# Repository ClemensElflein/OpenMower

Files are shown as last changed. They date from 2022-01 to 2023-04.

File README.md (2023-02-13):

# OpenMower - The DIY Smart Mowing Robot for Everyone

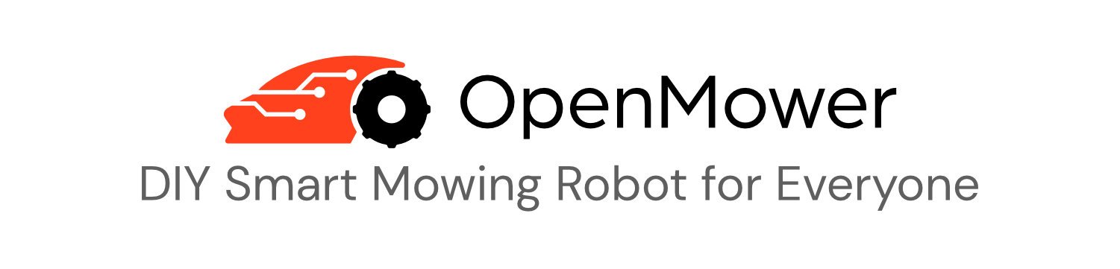
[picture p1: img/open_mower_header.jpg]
OpenMower the DIY smart robot mower
 

# Join the Discord server for OpenMower discussion: [HERE](https://discord.gg/jE7QNaSxW7)

*:warning: DISCLAIMER:**

**IF YOU ARE NOT 100% SURE WHAT YOU ARE DOING, PLEASE DON'T TRY THIS AT HOME! ASK IN [DISCORD](https://discord.gg/jE7QNaSxW7), IF YOU HAVE ANY QUESTIONS!**

# This project is active!
This is the hardware repository, so it might seem that the project is inactive, since hardware is pretty stable by now.
Most of the development work is done on the ROS code here: https://github.com/ClemensElflein/open_mower_ros

# About the Project

If you want to see a quick overview, you can check out this video:



Let's be honest: The current generation of robotic lawn mowers sucks. Basically all of these bots drive in a random direction until they hit the border of the lawn, rotate for a randomized duration and repeat. **I think we can do better!**

Therefore, we have disassembled the cheapest off-the-shelf robotic mower  we could find (YardForce Classic 500) and were surprised that the hardware itself is actually quite decent:
- Geared sensored brushless motors for the wheels
- A sensored brushless motor for the mower motor itself
- The whole construction seems robust, waterproof and all in all thought through
- All components are connected using standard connectors, therefore upgrading the hardware is easily possible.

The bottom line is: The bot itself is surprisingly high quality and doesn't need to be changed at all. **We just need some better software in there**.

## Project Goals

Here is a quick overview of this project's goals:

:heavy_check_mark: **Autonomous Lawn Mowing:** Obviously, the device should be able to mow the lawn automatically.

:heavy_check_mark: **Good Safety:** The device must be safe, e.g. emergency stop if lifted or crashed.

:heavy_check_mark: **No Perimeter Wire Needed:** We want to be flexible and support multiple mowing areas.

:heavy_check_mark: **Low Cost:** It should be cheaper than a mid range off-the-shelf product

:heavy_check_mark: **Open:** I want to share knowledge and enable others to build an OpenMower as well.

:heavy_check_mark: **Nice to Look At:** You should not be ashamed to have an OpenMower mowing your lawn.

:heavy_check_mark: **Avoid Obstacles:** The mower should detect obstacles and avoid them during mowing.

:heavy_check_mark: **Rain Detection:** The device should be able to detect bad weather conditions and pause mowing until they improve.

# Open Mower App

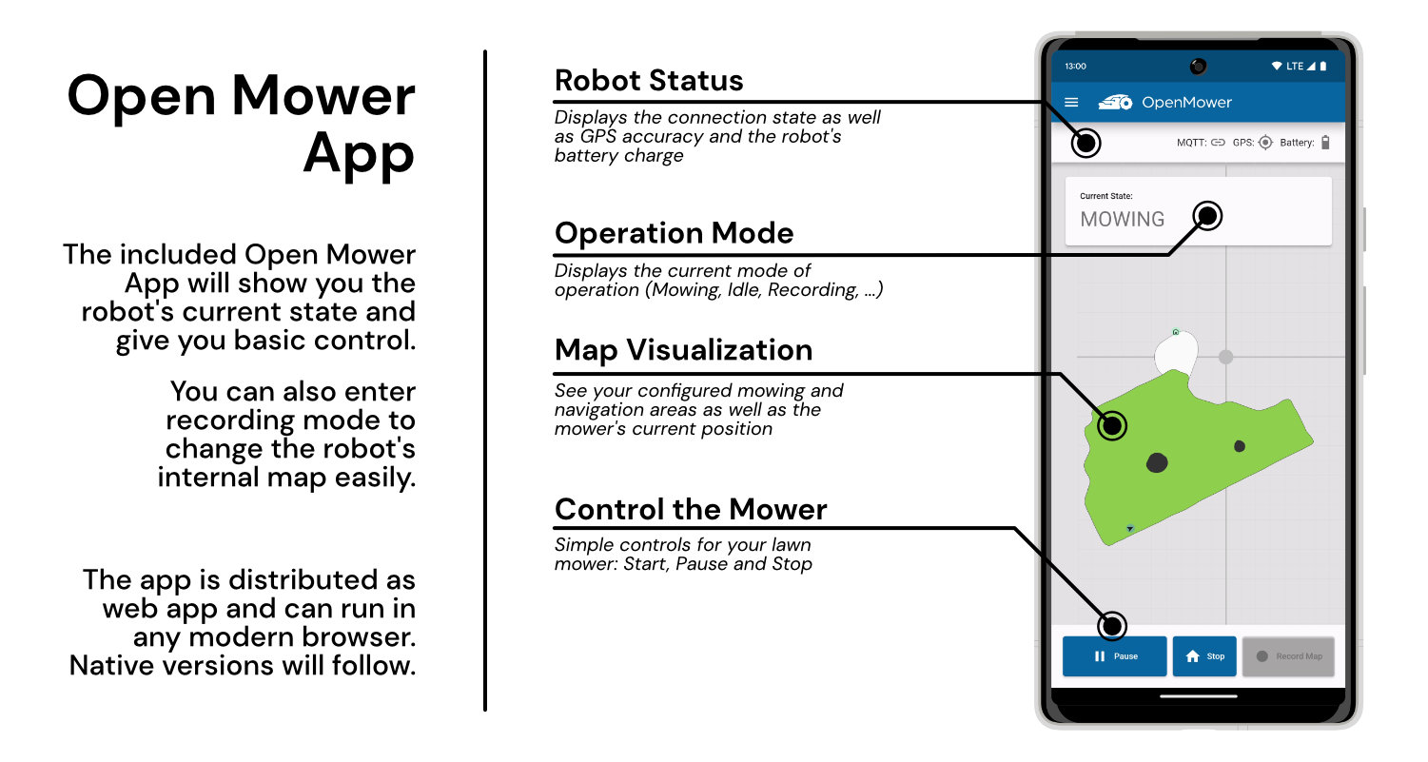
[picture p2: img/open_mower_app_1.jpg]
Open Mower App 1


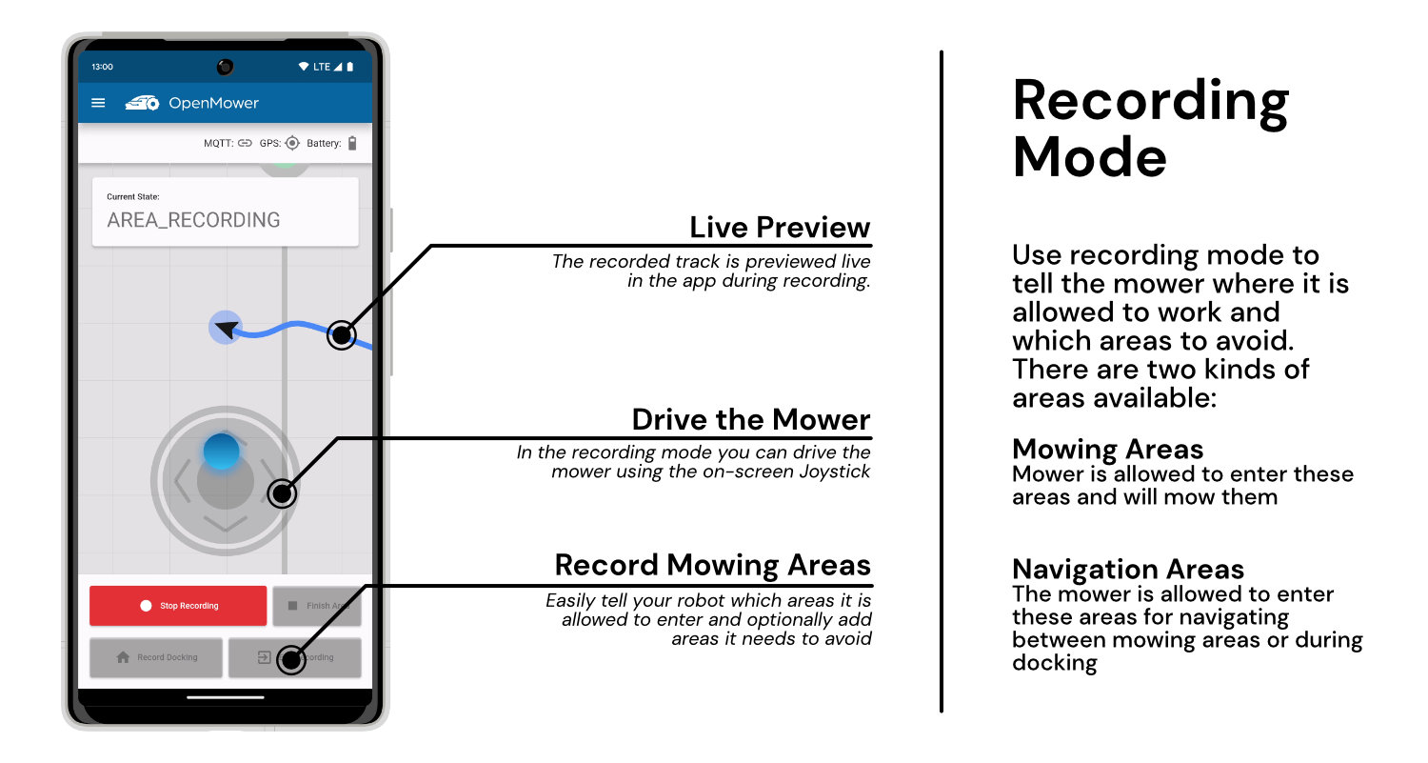
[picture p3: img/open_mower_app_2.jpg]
Open Mower App 2


## Current State

The basic mowing function finally works! As you can see in the video, map teaching and mowing work as expected. It even returns to the docking station automatically as soon as the battery gets low and continues once it's recharged.

At this point I can recommend that brave tech savvy users can build one for themselves! Since it's quite an expensive and complex project, please don't be shy and ask if you have any questions. I'm glad to help 🙂

### Hardware

By now we have a stable revision of the mainboard as well as two motor controllers to go with it. The [xESC mini](https://github.com/clemensElflein/xesc) and the [xESC 2040](https://github.com/clemensElflein/xesc2040). I'm currently using the xESC mini for my builds and it works very well. The problem with this controller is, its parts are currently hard to source. That's why we created the xESC 2040 based on the RP2040 chip. This is the low-cost variant and its support is currently experimental.

#### Hardware To-Do:

- [x] Low Level Firmware Implementation
  - [x] Voltage / Current Sense
  - [x] Emergency Stop Button tracking
  - [x] IMU Communication
  - [x] Rain Sensor
  - [x] Charging State
  - [x] Sound Module
  - [x] UI Board Communication
  - [ ] Discharge current for more accurate battery charge estimation
- [X] ROS Hardware Interface

### Software

The basic software is basically done; Our prototype works as intended (but is not able to avoid obstacles yet).

The software for the robot can be found in a separate repository: https://github.com/ClemensElflein/open_mower_ros

#### Software To-Do:

- [x] Mowing State Machine (Docking / Mowing, ...)
- [x] Path Planning
- [ ] Obstacle Avoidance
- [x] App / Visualization

## Getting Started

If you want to read how to get started building a robot for yourself, check the [OpenMower Website](https://openmower.de). There you can find information on which parts to buy, how to install the software and so on. If you find anything missing, please join the Discord server and ask there. Also there's the [OpenMower Wiki](https://wiki.openmower.de) which is written by the community. It has some additional guides and information.

# How You Can Help

You can help by starting an OpenMower build of your own. This helps to validate the concept and helps to create useful documentation for new users.

Additionally, you can help by starring 🌟 and watching 👀 this repository, since it will help with visibility. You can also subscribe to my [YouTube channel](https://youtube.com/c/ClemensElflein).

## Compatible Robotic Mowers

While disassembling the bot, I wondered about its mainboard: Instead of "YardForce" it read "GForce". After checking the internet for "GForce" robots, I found that that very similar looking robotic mowers are sold under the Herkules brand. Naturally I tried to dig deeper and actually found evidence that the mainboard is manufactured by some chinese company (SUMEC Hardware).

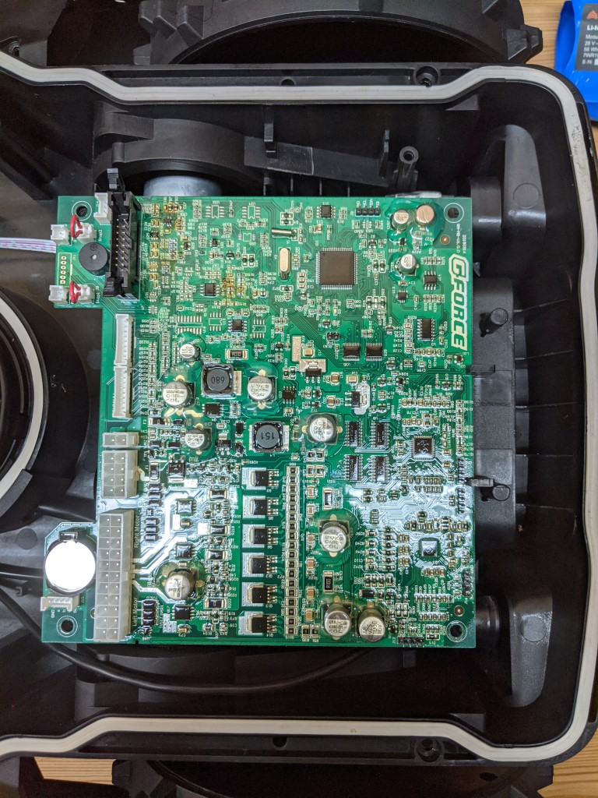
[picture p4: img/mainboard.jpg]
GForce Robot Mower Mainboard


It is therefore quite safe to assume that many robot mowers are basically the same device in a different case. This would be a huge win for the community, since this would mean that by making one of those robots smarter, we could upgrade lots of robots.

Therefore it might be a good idea to start a list of compatible devices. So if you have a cheap robotic lawn mower, you can check, if it was already disassembled in the list below. If it's not there, it would be nice of you to check, if it contains the same mainboard as ours and add your robot to the list with some some pictures / model numbers.

### List of Compatible Mowers

By now, some guys have disassembled their mowers and it doesn't look as good as I initially hoped. The GForce boards are basically just used by YardForce and some rebranded versions for the EU market. My exact hardware was only found in the mower I'm using (YardForce Classic 500) and in recently manufactured SA650 ECOs. The SA650 has a different chassis and we don't have a way of mounting the GPS antenna yet. Therefore at the moment, the only compatible mower is mine (the YardForce Classic 500). 

If you want to have a look at the disassembled mowers, check the Google Docs [here](https://docs.google.com/spreadsheets/d/1BX0-KEs5v-VED8-RA4BLE-wRdXHtlmcKy4n9K5vJVAA)

# More Infos

This page only contains the basic overview of the project. To follow my current development state, check out my [Blog](https://x-tech.online/).

# Patents, Local Laws, Liability
Before building a robot based on the designs published here, please make sure that you are allowed to do so in your specific regions.
There may be patents and / or laws prohibiting you of doing so.

The code/schematics/PCB files are distributed in the hope that it will be useful, but WITHOUT ANY WARRANTY; without even the implied warranty of MERCHANTABILITY or FITNESS FOR A PARTICULAR PURPOSE.

This basically means: I'm just documenting a project of mine here for free and I don't have the time and resources to check that devices built using this information will be safe to use, legal to use or even work as intended. You will need technical know-how to use this project and I'm not liable for any damages your devices do to anyone or anything.

# License

<br />This work is licensed under a <a rel="license" href="http://creativecommons.org/licenses/by-nc-sa/4.0/">Creative Commons Attribution-NonCommercial-ShareAlike 4.0 International License</a>.

Feel free to use the design in your private/educational projects, but don't try to sell the design or products based on it without getting my consent first. The idea here is to share knowledge, not to enable others to simply sell my work. Thank you for understanding.

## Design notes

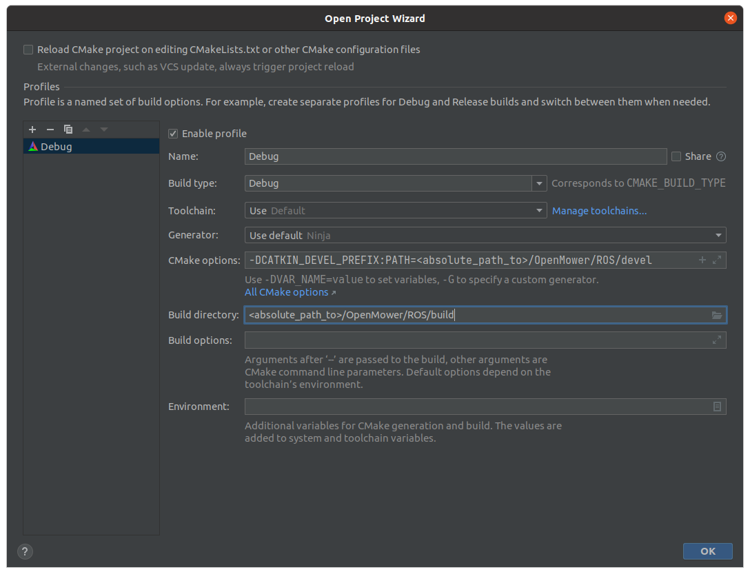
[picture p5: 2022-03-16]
img/clion_cmake_settings.png

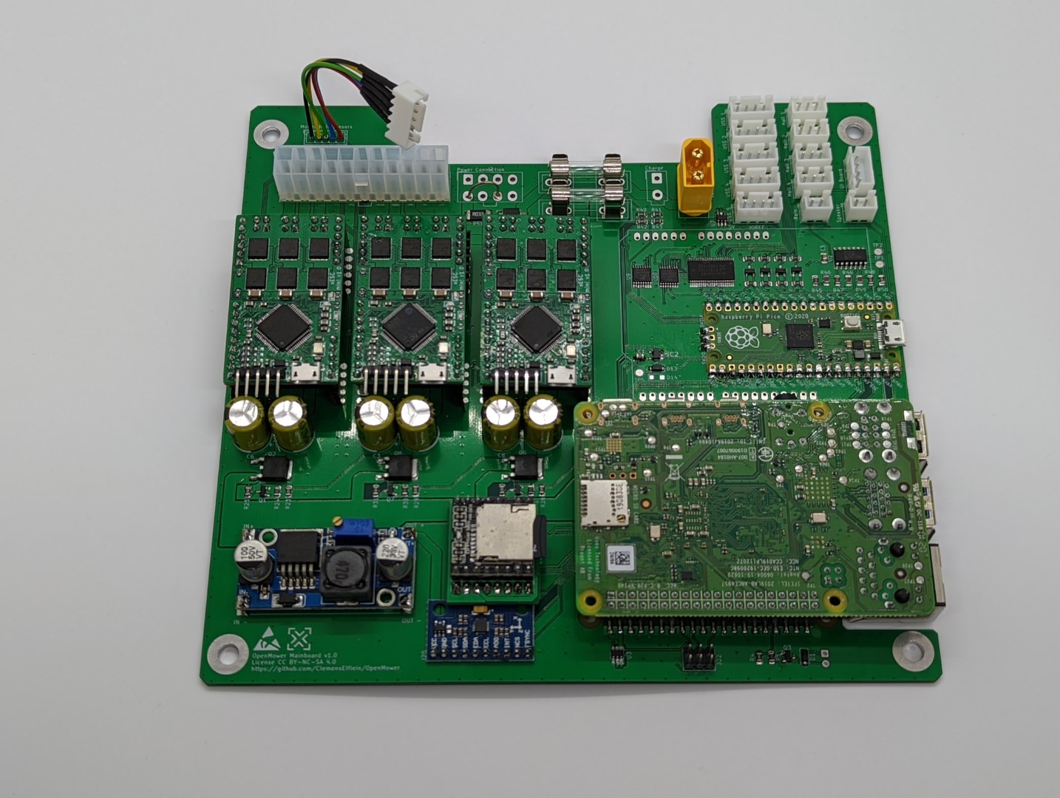
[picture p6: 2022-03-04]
img/open_mower_mainboard.jpg

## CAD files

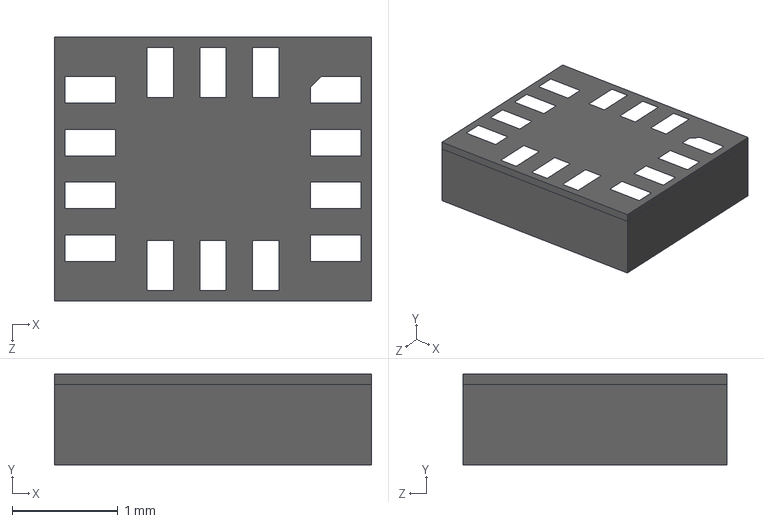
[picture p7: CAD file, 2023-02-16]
Hardware/OpenMowerMainboard/LSM6DSOTR/LSM6DSOTR.stp
3.00 x 0.86 x 2.50 mm

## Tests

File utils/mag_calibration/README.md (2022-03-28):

# Magnetometer Calibration

In an ideal word, when we rotate our robot around the Z axis, our magnetometer values would create a circle around the origin. Unfortunately, in the real world, due to magnetic fields in the robot and sensor bias, this is **not the case**. The magnetometer will most likely be an ellipse or a circle with some offset from the origin.

**This calibration will remove this offset, but won't remove any elliptical form!**

## How I'm currently doing this

Currently, I am doing it in the following way:

1. Put the robot in your lawn (turned on, fully assembled)
2. Start a teleop + recording session. Rotate the robot slowly in one spot for several rotations.
3. Run the plot_mag.sh script: `./plot_mag.sh /path/to/your.bag`
4. Check in the interactive plot, if your values are circular and if the fitted circle (red circle) is a good fit.
5. If everything seems fine, your bias values will be printed in the console (see example below).

## Example

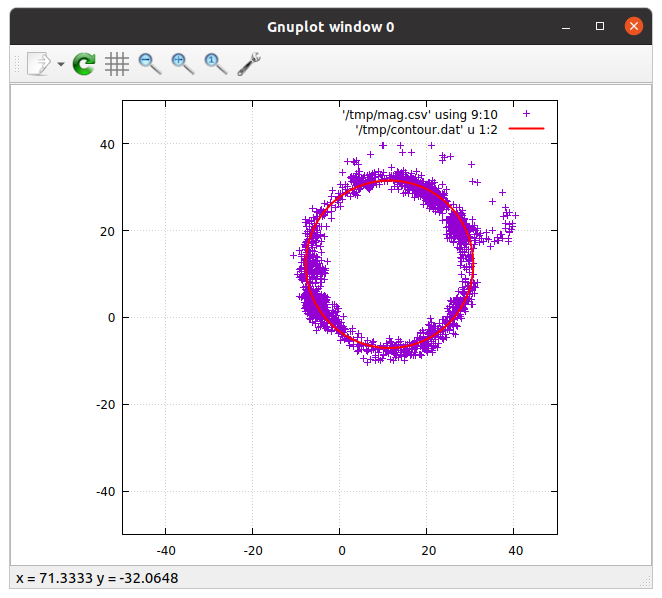
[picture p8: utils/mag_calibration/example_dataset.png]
example_dataset


This is the output of my calibration run today.

Note that:

1. The outliers have been rejected
2. The plot is pretty much a circle, moved to the upper right hand side

The console output was the following:

```bash
[...]

After 3 iterations the fit converged.
final sum of squares of residuals : 8.48886e+07
rel. change during last iteration : -4.36383e-06

degrees of freedom    (FIT_NDF)                        : 16540
rms of residuals      (FIT_STDFIT) = sqrt(WSSR/ndf)    : 71.6402
variance of residuals (reduced chisquare) = WSSR/ndf   : 5132.32

Final set of parameters            Asymptotic Standard Error
=======================            ==========================
bx              = 11.4452          +/- 0.0209       (0.1826%)
by              = 12.2336          +/- 0.02425      (0.1982%)
r               = 370.698          +/- 0.5595       (0.1509%)

correlation matrix of the fit parameters:
                bx     by     r      
bx              1.000 
by             -0.402  1.000 
r               0.092 -0.020  1.000 
```

**--> Our bias parameters (bx, by) are 11.4452 and 12.2336**

## Better Calibration

This assumes that the result will be a circle with an offset. In reality, the result could be an ellipse. Also it would be nice to automate this process.

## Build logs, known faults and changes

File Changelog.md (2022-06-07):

# Changelog

## [current dev progress]

#### Hardware

- Added solder jumper so that we don't need to solder some ICs if we don't need ultrasonic and sound
- Moved some solder jumpers to the bottom of the board to keep them accessible even with IMU mounted.

#### Software

##### Breaking Changes

- Moved most of the configuration to an external file
- Removed start and pause mowing from rosparams. This was just a hack to trigger it using rqt_reconfigure.
- Removed area_recorder and corresponding configs
- Added SensorFusion with imu_filter_madgwick, you need to set your mag biases in the global settings file now

##### Features

- Added UI Board integration to LowLevel Firmware
- Added service to start and pause mowing as well as start area recording mode
- Added area recording behavior to main logic, so that we don't need an additional launch file for it
- Added a mower_logic/current_state topic which has the identifier of the current high level state.
- mower_comms now listens for UI button messages and calls the high level control service accordingly.
- Added support for LAT/LNG coordinates instead of relative coordinates. Set **OM_USE_RELATIVE_POSITION** to **false** for this and provide an origin for your local coordinate space using **OM_DATUM_LAT** and **OM_DATUM_LONG** in your local config file.
- Added the mag_calibration node to help magnetometer calibration without manually recording and copying files.

##### Small Fixes

- Changed planner logic, so that it starts with innermost outlines

- We can now configure arbitrarily many outlines
- Motor temperatures can be configured
- Added safety offset parameter to the outline (i.e. shrink area without rerecording the areas)
- Added vesc_msgs to mower_msgs to resolve a dependency issue

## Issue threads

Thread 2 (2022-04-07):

Website SSL Error

admbradford, 2022-04-07:
Receiving an `ERR_SSL_PROTOCOL_ERROR` when visiting your blog site https://x-tech.online/

ClemensElflein, 2022-04-07:
Thank you for the report. It's working fine for me even in a private tab. Which browser are you using? What's the error message you're getting?

admbradford, 2022-04-08:
I’m on mobile chrome v100.0.4896.77 iOS 15.4.1

here’s a screen shot

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

admbradford, 2022-04-08:
I checked off my home network and it worked fine, I have some aggressive protection from my router. It’s likely due to the second cert

[SSL Server Test: x-tech.online (Powered by Qualys….pdf](https://github.com/ClemensElflein/OpenMower/files/8451909/SSL.Server.Test.x-tech.online.Powered.by.Qualys.pdf)

ClemensElflein, 2022-04-08:
Thank you for the info! I'm looking into it. To be honest, I'm just using the Let's Encrypt Certbot and was glad that it seemed to work out. There has to be some strange configuration still.

Closed 2022-09-22.

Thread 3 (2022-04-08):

Option to mow in a randomized pattern?

jh83, 2022-04-08:
Is it possible to have the mower to cut the grass in a randomized pattern  and only use the perimeter as a "limit" for which it should stay within?

Having the mower cut on the same lines over and over again will create track's in the lawn. There is a reason to why husqvarna has spent a lot of time developing how the robot should find its way back to the charger, where it actually varies its distance to the perimeter cable to avoid creating track's.

Husqvarna has now released a gps rtk version of its automower (which is very expensive) and I think that stiga will release one soon as well.  As far as I know, this still cut in a randomized pattern, while using gps for the perimeter limits.

Very good project though!

R5fan, 2022-04-11:
If you want to avoid making "tracks" or stripes (which many people try to make on purpose btw), the much better solution is not reverting to random navigation, but randomizing either the starting point (so tracks are offset a bit on each session, although with the narrow mowing width of most robots that may not yield much) or rotate the orientation of the tracks by a random angle.

jh83, 2022-04-11:
A robotic lawn mower does not create the "stripes" which many People (including me) like even if it would cut in a straight pattern.

I agree on the inefficiency in the randomized pattern. But there is a reason to why the GPS mowers are sticking to the randomized (which not really is randomized) pattern on their rtk-gps models.

A robotic lawn mower, when used as intended, creates a much nicer lawn compared to a normal cutter. The reason behind it is that the robotic "always" cuts and does it from different angles. Moss and other none-grass things does not like it, and is replaced by the grass. - So there are different views on what a robotic cutter is, if it is intended to cut the lawn as quickly as possible, or if it is intended to "take care" of the lawn.

If running on straight lines, then care needs yo be taken to the uncut grass that remains when the wheel presses down rhe grass, and then is unable to cut that grass on the next line and so on.

Here is an interesting article on the line vs random cutting. It says that there is only a 30% time difference between the two. https://robolever.com/random-vs-systematic-robotic-mowers-which-is-better/

As said. We like things differently, so If it would be possible to run either straight lines, or in a random pattern and use gps for perimeter then it would be great

pbs-websuntangled, 2022-04-11:
Agreed 👍

R5fan, 2022-04-11:
Mowing from random angles matters, but systematic mowing with a randomly rotated pattern every session would yield the same result. I dont see the downside. Heck, since his code uses slic3r code, you can even use any other infill pattern you want, plenty to chose from, all of them far more efficient than random.

Speaking of efficiency, if you have a square lawn with no obstacles, _maybe_ the 30% less efficient claim is right, but for sure its not in my garden, where my robot can mow for 3-4-5 days and still not cover every patch. If it mowed systematically, knowing its width and estimating speed, I guess it would take ~3-4 hours?  Even if its 24hr, that is a massive difference. I used to have a random navigation robot vacuum, and that is okay, because you cant tell if it "missed" a spot for a few days. Lawn mower is different, if you cant mow for a week due to rainfall, and then it takes almost a week before the robot to "catch up" and get everywhere. So during that  week you will have patches of freshly mowed grass next to nearly 2 week growth, not very pretty. More than once I took my old mower and mowed my lawn by hand to avoid exactly that.

Anyway, if that is what you want, who am I to stop you, but it makes no sense to me.

pbs-websuntangled, 2022-04-11:
For me the point is not so much about wanting randomness

Rather it's good to cut the grass from different angles with different patterns

It's definitely true that for real world lawns, it can be 4 or 5 days of permanent mowing before the same hit is hit twice

Structured mowing with  rotated efficient row by row mowing would be a great feature

This project is amazing 👍👍👍

R5fan, 2022-04-11:
> Structured mowing with rotated efficient row by row mowing would be a great feature

Agreed! Because random navigation doesnt result in even distribution. To illustrate, here is my back lawn:
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
The visible tracks give a hint (I would really LOVE to create a coverage map somehow from my timelapses, or even be able to simulate random navigation on my lawn and see the result, im just curious what the coverage looks like, and I know its not evenly distributed);  the mower will cross the center of the image dozens of times before ever reaching the left corner. I also really do not like the "look" of those tracks. They fade, but if you mow every day, they are there every day especially if its a bit humid.

kevinmce, 2023-06-30:
There is a mow pattern orientation in the mower config, this should be relatively easy to have randomized at the start of each mow should the user input that option.

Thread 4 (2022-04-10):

How to start ti build the more?

chicco83, 2022-04-10:
Hi.
I'm very interested in the project but It Is not clear how to start the hardware part. Which parts to buy, if It Is mandatory to have a dedicated PCB produced ecc

r00li, 2022-04-13:
Yeah I too would be interested in a bit more detailed guide of what exactly needs to be purchased, which PCBs made, ...

I had a look at the BOM and it seems a bit incomplete - it seems to only cover the main board components, but doesn't include things like the GPS receiver, ...

GruNyv, 2022-04-16:
Based on the video he posted, the gps receiver is a simplertk2b (with a zed-f9p GNSS module) and a u-blox multiband antenna. These are relatively cheap, around 200 euros, considering that other brands usually cost several thousand euros.

Kisses99, 2022-04-17:
Maybe it's even cheaper to hook up an old smartphone.

GruNyv, 2022-04-17:
@Kisses99 The problem is that your smartphone is not RTK compatible. You need a GNSS module that supports RTK, such as the ZED-F9P.

Kisses99, 2022-04-17:
Ah got it.

GruNyv, 2022-04-17:
Yes, the cost of RTK certainly is a barrier to entry. This was especially true before the ZED-F9P, where it was mostly reserved for the industry and extreme hobbyists. Another issue is that you might need 2 of them, where one acts as a base station, if there are no freely available base stations near you through i.e. RTK2GO and you don't want to pay for a commerical subscription

FadeFx, 2022-04-17:
@Kisses99 there are cheaper optiins as well, but i guess they dont provide enough precission for a task like that. Did you ever check the precission of your smartphone gps? its most likely not below 5m...

GruNyv, 2022-04-17:
Unless you use some sort of differential gnss (which RTK is a subgroup of), you can't expect better accuracy than 3-10 meters depending on the conditions

Kisses99, 2022-04-17:
@FadeFx right that's what I just figured.  However I'm still concerned that gps accuracy may be significantly impacted by shades of trees.  For an open yard this may just be fine.

GruNyv, 2022-04-17:
Yes, the tree shades and building is what I am concerned with. I have been working with this exact model during this spring and it often has troubles when you enter non-open areas

FadeFx, 2022-04-17:
could it be possible to compensate this by also taking in account your actual movement?

GruNyv, 2022-04-17:
You certainly can predict your movement using multiple sensors using a kalman filter. However, it might work to simply drive randomly when you are in a region without signal, since this is what they already do. The issue is of course the possible lack of boundary wire

mischla, 2022-04-17:
> Yes, the cost of RTK certainly is a barrier to entry. This was especially true before the ZED-F9P, where it was mostly reserved for the industry and extreme hobbyists. Another issue is that you might need 2 of them, where one acts as a base station, if there are no freely available base stations near you through i.e. RTK2GO and you don't want to pay for a commerical subscription

Is the German SAPOS system which provides Ntrip in RTCM 3.1 format what would be needed here?

GruNyv, 2022-04-17:
@mischla Most network RTK providers which uses RTCM 3 should work, but you should check out which satellite configurations they provide corrections for (GPS, Galileo, GLONASS...)

mischla, 2022-04-18:
Thanks for the quick answer, in this case all of them.
Link below in German valid for NRW: https://gppspro.saposnrw.de/service.php

stilsch, 2022-04-18:
Maybe a look at ardumower.de and it's Sunray (GPS-RTK) firmware might also help you https://github.com/Ardumower/Sunray

Bojkas1985, 2022-04-19:
Hi, wouldn't some form of triangulation using bluetooth iBeacon be possible?

fsommer1968, 2022-04-19:
> Hi, wouldn't some form of triangulation using bluetooth iBeacon be possible?

What is the accuracy you can achieve?
Everything more than a few (more than 10cm) over the complete backyard is just not acceptable!

GruNyv, 2022-04-19:
From what I could find on the Internet, the accuracy is at best one meter, which is not good enough to be used for control. Could maybe be used as a backup if you add a safety zone on 1 meter from the perimeter when you don't have RTK, but it will of course increase the already pretty expensive build

lightheaded, 2022-08-07:
Hi! Coming back to the initial question, would it be possible to add a "getting started" section to the readme? I have extensive software background and I tinker with some electronics, but I've never created my own PCB. Looking at the project, I have the same problem as @chicco83 - where to start?

vamatis, 2022-08-10:
Have a look at the wiki. Most of the needed infos are there...
If in doubt, just ask in the discord

lightheaded, 2022-08-10:
Thanks for pointing me that way! Here's the link for those still lost: https://wiki.openmower.de/index.php?title=Main_Page#How_to_Get_Started

rfvermut, 2023-02-13:
There is a better guide now: https://openmower.de/docs/getting-started/

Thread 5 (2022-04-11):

WORX Landroid M WR140

TonyBrobston, 2022-04-11:
> Naturally I tried to dig deeper and actually found evidence that the mainboard is manufactured by some chinese company (SUMTEC Hardware).

This part of the readme got me curious to checkout the board in my WORX Landroid M WR140.

It looks like it's a completely different board; however, I figured since I took the pictures, I mine as well post them in case this mower can somehow be supported. If that is the case, I'm definitely interested in getting off Worx horrible software, it is quite unimpressive.

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

unreality, 2022-04-14:
Depending on whether that ESP32 runs the whole thing or just provides wifi/bluetooth connectivity you could reflash it quite easily with custom firmware.

The ESP32 is reasonably powerful for an embedded soc.

LTKingChaos, 2022-04-16:
I would also like custom firmware for the Landroid. Factory firmware sucks bigtime.

hugokernel, 2022-04-20:
Thank you for the pictures @TonyBrobston

I'm also very interested in an Opensource version of a Landroid (WR155 / L2000) in order to perpetuate the use of my robot and to bring additional features.

Seeing the electronic board and the fact that the board is embedded in resin will make it very difficult to repair.

The LandLord project (https://github.com/Damme/LandLord and https://hackaday.io/project/6717-project-landlord) is trying to produce an Opensource software for Worx robots (specifically the wg79X).

Damme, 2022-04-20:
Btw, the cpu is a LPC1768 under the goop (epoxy?)

RFBomb, 2022-05-06:
I have a 2021/22 model WR147 (with the radial dial for menu navigation), and I am also interested in this project. I also have the ACS unit installed, so support for that would be a must.

Michael-Bischof, 2022-05-07:
Also super interested in flashing custom firmware on the worx robot. I have the Landroid L (WR148E) and would also be into modding it. Can‘t get worse than it is right now software wise 😅

JochenKr, 2022-05-11:
Any chance that LandLord project and OpenMower will be combined?
OpenMower idea to use Rpi with good GPS is fantastic. This in combination with a simple modification of the Worx Landroid e.g. just connecting the Rpi to the original MCU to give the commands to the robot, would be a great simplification and super cost efficient

MBischof-gcx, 2022-05-11:
Already happening ;) See https://github.com/Damme/LandLord/issues/5

endoskop27, 2022-05-23:
Hi @TonyBrobston! Is there any Letters/Numbers printed on the big Controller on the Board (not the ESP32)?
On the pictures it is quite invisible

chopperpl, 2023-05-08:
Is this still alive? I would love to jump on the wagon, but it seems the shortage of RP boards and its price spike have killed the project.

mangeamg, 2023-05-24:
Why not use a cheap RPi clone, like orange?

scigany, 2023-07-12:
Hi,
does anyone have a diagram where I can identify the two elements marked with an arrow that are burnt in mine?
burned a hole in them,

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

Jmaxime89, 2023-07-29:
Hello ! I too would be sooo interested in supporting the landroid.

I keep an eye on the projet since a long time but the yard force is very hard to source in canada

pawster-hub, 2023-08-04:
Good morning,
I have a pcb in front of me with fried components. Can someone give the symbols of the elements t9, t10, t? (left of connector), d5, ic9? Hopefully I'll be able to do something more with it. Regards
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

shagi898, 2024-05-25:
Hi. someone found ic9
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

iLLiac4, 2024-06-09:
What is the purpose of this IC. The problem is that even when robot is turned off with the inserted battery the chip consumes power. I have checked it with thermal camera. This ic gets at around 30-40C. Also the coil gets a little warm. The problem is that it drains the battery even when not doing anything. Worx batteries has no overdischarge protection in them so it drains them fully.

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

Andy617237, 2025-03-24:
> Hi. someone found ic9 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

Hello, Someone find what is iC9 my is burned ;-(

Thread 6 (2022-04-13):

Alternative to custom PCB

conradkirschner, 2022-04-13:
Is there a possibility to remove the custom PCB and use "standard components" e.g. pi cluster ?

This would enable more people in development.

fsommer1968, 2022-04-13:
You have to integrate with the remaining parts like left drive, right drive, cut engine. I´m not aware of a pi that can direct connect :-) Therefore at some point you always need an integration component, you name it "custom PCB". I applaud the effort building the PCB because I´m sure it costs a lot of money.

conradkirschner, 2022-04-13:
Would be cool to have the research material why a custom PCB was required and where it could be possibily replaced.

I defenitly see the reason to use a custom PCB, it's just for enabling more devs if this step would be optional for production use ;)

r00li, 2022-04-13:
I mean these days where you can get a custom PCB made for like 5$ (a bit more for bigger ones, but still not that much) it's a no-brainer that a custom PCB will be used. I don't see why one would even want to go towards a different route.

ClemensElflein, 2022-04-13:
I agree, it's an obvious choice here. We need to connect hardware of some kind to interface with the robot and we need it to fit a predefined space. A custom PCB provides all that for very cheap.
I know that not everyone is willing to solder the SMD components, but that's a completely different issue. At the moment this is very much R&D so there's no way around it.

Closed 2022-04-13.

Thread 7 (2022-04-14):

Perimeters

nyxtom, 2022-04-14:
One issue that you may run into is that typically front lawns have neighboring lawns that you *would* want to designate a perimeter/border on. That being said being able to do this from the phone (i.e. AR) rather than wires would be preferred.

ClemensElflein, 2022-04-28:
You are able to set a perimeter by driving around it. Check the YouTube video for a demo: https://www.youtube.com/watch?v=BSF04i3zNGw

It's not as fancy as an AR app, but it works well for defining a boundary.

I'll let this open as a feature request, though.

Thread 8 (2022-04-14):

US/North American source for compatible base hardware?

aderusha, 2022-04-14:
As noted in the README, the existing platform is the Yard Force Classic 500 which comes from a Chinese OEM [SUMEC Hardware and Tools](https://www.sumecpower.com/) which itself is a subsidiary of [SINOMACH](http://www.sinomach.com.cn/en/).  Their ["Brand" page](https://www.sumecpower.com/brand) lists G-Force, Yard Force, and PowerG.  PowerG looks to be battery powered hand tools, which leaves the G-Force and Yard Force side of things.

## Yard Force USA

The Canadian and US links from the SUMEC page bring you to [YardForceUSA.com](https://www.yardforceusa.com/).  They have a [Robot Mower product page](https://www.yardforceusa.com/robot-lawn-mowers) with two products listed, the RVX4E and RVX4.  I can find no mention of these devices being made available for sale anywhere.  I've emailed the US distributor and will update if I get an answer back.  I eventually found [an online shop for Yard Force tools in the US](https://sumec.mybigcommerce.com/force-tools/) but no robot mowers are listed.

The [international page for Yard Force](https://www.yardforce-tools.com/PC_Web/International/HTML/Products.html) lists different models than the NA page, and that includes a model [SA500ECO](https://www.yardforce-tools.com/PC_Web/International/HTML/Products_parameter.html?id=598) which bears a passing resemblance to the Classic 500 (as well as being suspiciously similarly named).  [Amazon in the UK](https://www.amazon.co.uk/Yard-Force-Robomower-Lithium-Ion-SA500ECO/dp/B07B6WHCYQ) shows this model as no longer available and it appears to be an older 2018 device which they possibly are no longer making.

## G-Force

This line is harder to pin down.  [The product page](https://www.gforce-tools.com/en/RoboticMower-26.html) shows a handful of models, but I cannot find any listings for these mowers on sale anywhere.  [Product videos I've found are from 2015](https://www.youtube.com/watch?v=HbvwlFQ7TGM), so this might be an older line of devices.

---

If anyone else has any ideas as how to obtain a suitable mower deck in the US, post here and we can all get to hackin'!

llama, 2022-04-22:
I am planning to order from [amazon.de](https://www.amazon.de/M%C3%A4hroboter-Classic-500-Kantenschneide-Funktion-Wochentags-Bedienfeld/dp/B08H1Y3KXZ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)  and use [mygermany.com](https://account.mygermany.com/web/content/new-register?canvassID=cdbe1208-010e-47b1-9c4d-8b1bb678f9e4) to forward the package.

The question I have: do all of the models on that Amazon.de page work with OpenMower? Or should I buy the "Classic 500" to exactly match what @ClemensElflein has done.

rjt, 2022-05-25:
$590 New up on eBay.  Buying thru PayPal may offer some protection even though [drahman7](https://www.ebay.com/usr/drahman7/) is a member of this project.  [https://www.ebay.com/itm/304477543176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](YARD FORCE robot lawn mower Classic 500, 500 m², 40% incline, works w OpenMower)

[https://www.ebay.com/itm/304477543176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](https://www.ebay.com/itm/304477543176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)

darkmastermindz, 2023-04-14:
Any updates on this?

ffries, 2023-07-10:
If you visit Amazon in France, you should be able to find the product number (ASIN). I did the converse many times. The ASIN number is B09RFVFV1C. Then connect amazon.fr and try to buy it.

Here is a full URL:
https://www.amazon.fr/Yard-Force-Tondeuse-Classic-Bluetooth/dp/B09RFVFV1C/

Please note that I did not purchase it myself and I am still waiting.

symmatree, 2024-04-15:
I can't find the Yard Force 500 Classic for sale on any site now. I'd guess some other chassis would work but it's not at all clear how to validate that?

liquidbear99, 2024-08-03:
@symmatree I also am unable to see it sold anywhere
on any site. (North America or Europe) The classic 500 may be discontinued.

mpcathey, 2025-06-26:
I'm in the same boat.  Has anyone else had better luck?

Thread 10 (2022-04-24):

Avoid filesystem corruption

vguttmann, 2022-04-24:
I would very much like to build the mower and help with development, but for me to build it, it needs to be foolproof long-term, as I will be moving out soon, and I don't think my parents have any interest in reinstalling the operating system on their lawn mower.

Raspberry Pis have a history of corrupting the file system on their SD cards, so I'd like to know if there are any mitigations for this, and if not, advocate for their implementation.

Schaumi19, 2022-04-25:
As far as I know the OS is still Raspbian with ROS installed. The Problem with the SD-card is writing and in Raspbian there is a option to not write to SD. If that is selected it writes only to the RAM so if there is a power loss the system is set back to the point the option was selected.
Hope it helps

noobydp, 2022-04-29:
I got bored and read up on this problem, so I'm no expert.

[This article](https://hackaday.com/2022/03/09/raspberry-pi-and-the-story-of-sd-card-corruption/) suggests the problem has been resolved and may have been due to bad rpi hardware or cheap sd cards.

I've used 3 or 4 pi's over the past few years starting with a Pi B, and I've never had an issue.
I've always Used genuine samdisk cards, not sure if it helps.

That said the overlay fs/ read only sd card mode is handled at the os level in raspbian so might be an option.

scottishjohn1982, 2022-04-29:
The Amazon warehouses in the us are full o of "legitimate" sd cards from
major brands that are actually produced there manufacturer but are part of
lots that failed qc and somehow (through illustrated supply chains) work
their way in to the Amazon warehouses and get mixed back into the
legitimate supply chain.

I have a stack of sd cards that I paid good money for that I only used for
projects that can run in read only mode.

There were issues with the older pis that could easily corrupt quality sd
cards, but those have been resolved.

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

Schaumi19, 2022-04-29:
It is true that you have less problems with genuine sdcards whatever brand, but it is also a fakt that the life time of an sd card is limited tue to the write cycles(up to 10k some sources say 100k). Thats why the problem is not the normal usage. But if there is something like a log file that gets written every second you are done afer a few days. Or if the file gets writen less the problem occers afer a longer period of time what could be worse.

FilipBE, 2022-04-30:
Some Raspberry Pi Compute Module 4 (CM4) boards come with a built-in eMMC flash chip for storing nonvolatile data. This chip replaces the need for a separate SD card, which can be useful if you want to avoid the use of SD cards.

JoeKae, 2022-04-30:
Just boot from a small ssd via usb. They last much longer than sdcards or emmc.

FadeFx, 2022-04-30:
i am not sure if adding an ssd inside the smal case of a mower.

JoeKae, 2022-04-30:
You can use small m2 type ssds.

vguttmann, 2022-04-30:
I did open this issue because I had a (as far as I can tell) genuine Samsung 64GB SD card go bad in a Pi that a personal project ran on.

I would agree that a CM4-based mower sounds like a good idea, given the onboard eMMC flash, and that it is intended with use in industrial settings in mind. Of course, that would mean sacrificing USB 3.0 connectivity, but as far as I can see, that's not really used here.
The CM4 DOES have a USB 2.0 interface, so no USB controller on the board would be necessary.

pedromorgan, 2022-05-04:
At end of day we want machine to be 100% reliable.. with ..a failover etc...(line replacable)

maybe an SD raid ? or ssd RAID ?
as @JoeKae mentions, the m2 ssd's could be useful.. but expensive..

or a stpuid raid..
https://hackaday.com/2018/02/12/worlds-stupidest-solid-state-disk-drive-hack/

Schaumi19, 2022-05-05:
ssds last longer but have the same problem. So just dont write do the ssd/sd or only write every few days. I don't think it is a real problem, that it gets reset a few days if the battery dies.

wooter, 2022-06-21:
I've been using [Log2Ram](https://github.com/azlux/log2ram), and endurance type SD cards. None of them have failed yet, in other applications like RPi dash cams and power monitoring.

ClemensElflein, 2022-06-21:
We're working on having the software as docker images, so that we can use Raspbian as base system. This would allow us to use the overlayfs setting in raspi-config which should fix the sd corruption problem without much work.

plopaur, 2022-08-08:
I would recommend looking at Tinycore Linux for Rasperry Pi. This is a minimal ramdisk only distribution with no automatic writing to sdcard which i have used in the past. A new package for openmower has to be created.
Configuration changes can be written to sdcard instantly.

http://www.tinycorelinux.net/ports.html

docgalaxyblock, 2022-08-31:
@plopaur I could not find any information if ROS runs on TinyCore. If it does and it is stable that may be a way to do it

@vguttmann @pedromorgan I am planning to build my mower based on a CM4 w/ emmc and [this adapter](https://waveshare.com/wiki/CM4-IO-BASE-A) - It has a M.2 2230/42 slot too but I think a ssd is an overkill

It will take some time cause I accidentally ordered a CM4 w/o wifi so I am returning it and need to wait until my desired variant is available again.
Also I plan to take a look around the OS side of the project
*Stay tuned* 🤗

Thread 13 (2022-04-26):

Cutting grass in different pathways

Frosty21, 2022-04-26:
More of a feature idea but when cutting grass you wouldn't want it to cut the grass the same way every time. So cutting it at 4 different angles (horizontal, vertical and diagonals) would be a good idea. That way you avoid ruts [ref](https://www.scotts.com/en-ca/library/spreaders-mowing-tools/how-mow-lawn-lawn-mowing-tips-tricks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,forming%20ruts%20in%20the%20lawn.) [ref2](https://blog.davey.com/2019/08/should-i-alternate-directions-each-time-i-mow/)

dunno how you would implement this but if I have time later in the year I look into it from your code.

btw nice work @ClemensElflein . Maybe from this we can implement this as a snow remover (just an idea on top of this way out of left field...). would be cool if you could add another motor to horizontal attaching a snowblower scraper and the flat motor as a fan blower with a controlled vent that could store the snow in a certain area.

patrickdk77, 2022-04-29:
Is the gps accurate enough that it would ride in the same 1" wheel width track each mowing? Relative accuracy is pretty good, for position of a single mowing, but between days, or even hours, it should drift by a good foot or so, causing it to not rut.

staysayo, 2022-05-08:
Yes, it's very accurate because he's using RTK positioning that's accurate to 2 - 5cm (3/4" - 2").

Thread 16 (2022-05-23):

Enable Low Level Emergency Deactivation (Button)

endoskop27, 2022-05-23:
**Problem Statement:**
Since the Mainboard of the Robotic Mower has been substituted the emergency Stop button functionality is assumed not to be working. This part is one of the most important safety measures beside the Gyroscope based deactivation of the mower, I propose to integrate a low-level emergency switch which deactivates the Motors.

Expected Behavior:
- If Emergency Button is pressed the Robot stops mowing instantly and requires manual reset
- The low Level Controller (PiCO or similar) requires an reinitialization routine from Raspberry in order to restart operation
- Saving the location and time of event on storage

Proposed approaches:
- Hardware based Kill-switch cutting the motor driver voltages
- Software based ISR listening on the Emergency Button Pin and actively deactivates motors

ClemensElflein, 2023-06-28:
your assumption is wrong, the emergency button works as you describe. mower goes into emergency and needs to be unlocked manually

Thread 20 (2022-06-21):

Versioning / Branches / Releases

ClemensElflein, 2022-06-21:
At this point it would be nice to think about release + versioning, since it's not optimal right now.

**Current State**
Currently, I'm just pushing updates and we're using the latest development state. This is fine for now, because I try to only push things that are working, but in the future it might be nice to have a "stable" release.

**Goal**
Since the OpenMower is basically two components, the hardware and the software, it would be nice to have a versioning system which shows which hardware version works with which software version.

Also it would also be nice to provide a packaged bundle of hardware (BOM, Gerbers,...) and software (precompiled image).

**Progress**
**Vermut** on my Discord is working on streamlining the KiCAD releases and **jakub** is working on streamlining software releases.

Currently the idea for hardware is to have a GitHub action which checks DRC, packs gerbers, generates iBOM, etc. This solves the problem of people just wanting to get Gerbers + BOM to order the PCBs without getting into KiCAD. This also prevents me from forgetting to generate the artifacts.

For the software the idea is to have a GitHub action to pack a docker image. This allows people to quickly get the software, they won't need to compile + it's easy to upgrade.

This issue is meant for discussion about where to go from here basically.

ClemensElflein, 2022-06-21:
+ jakub and I are thinking about removing the link between the repos and only having the final stable software image here. If someone wants to develop, they should get the other repo for the sources.

rfvermut, 2022-06-21:
DRC/ERC checks can be per-commit, CI style. And everything like linters, code-style, compilation attempts.

And artifacts can be published/generated per tag.

ClemensElflein, 2022-06-21:
So basically as I understand it, we're doing the following:
- For the current master state, a GitHub action builds software and hardware artifacts. These should be used for development purposes / latest feature testing only and should not be considered stable.
- Since the software repo will be decoupled from this one, it will also build a Docker image for the latest master "unstable" version.
- For a stable release, we'll create a tag and the user knows the latest tag will be a stable version.

The question is: How do we get this to synchronize? I.e. each "stable" OpenMower release will probably consist of software and hardware artifacts.

Do we manually create software and hardware releases independently in the two repos and using the version number, the user can get compatible versions (i.e. all 1.x hardware versions will work with all 1.x software versions) or do we somehow synchronize the repos and pack everything together into one big (hardware + software) release bundle here?

When packing everything together and we're just doing a software release, this would probably mean that new release will copy the older versions of the hardware with a new version number on it (I don't like that, because the same exact PCB will be stamped with different versions).

So I'd go with different releases sharing a major version.

jkaflik, 2022-06-22:
I don't have any experience with hardware release process lifecycle, however I believe hardware will have much more less frequent release process.

I believe we will have dozens of iterations on software for only one change on hardware. Additionally, there is an idea ROS stack will support more than OpenMower's mainboard. We already have @ClemensElflein 's board and @cloudn1ne 's Mowgli custom firmware for c500.

IMO we should have hardware & software with an independent release cycle. This will require us to keep some kind of "contract" alignement and think better about the breaking changes later. Sharing same major version is good idea.

ClemensElflein, 2022-06-22:
I agree and I'm trying my best to keep the API stable. But since it's still in development (there is not really a stable software to begin with), the API might still change. I'm sorry for the larger breaking changes, but they were necessary to simplify configuration and to support more hardware configurations.

Great work on Mowgli btw!

cloudn1ne, 2022-06-22:
cool im gonna check out your code and will try to understand it as much as possible and then setup some kind of middleware proxy services - maybe at some point we can make adjustments to make life easy for eventual other hardware.

i have some kind of capabilities announcing schema in mind atm. if one day OM hooks into that, other hardware should be easy to support as long as it supports some minimum reqs and adheres to the ROS REP stds

Closed 2022-08-19.

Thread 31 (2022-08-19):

WT901 overflow issue

ClemensElflein, 2022-08-19:
If the magnetic offset of the WT901 is too large, the values will overflow or clip. This way the orientation in the open mower software will be nonsense.
The solution is to move the WT901's offset register in such a way that the values are in a sensible area. We should probably detect the overflow somehow and move the offsets accordingly.

ClemensElflein, 2022-08-19:
Example of the overflow:
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

Example of clipping:
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

Example of a good magnetometer plot:
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

ClemensElflein, 2022-11-07:
closing this, since we don't need the magnetometer anymore

Closed 2022-11-07.

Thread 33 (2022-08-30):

Is there a way to adjust blade height?

vipasane, 2022-08-30:
Actually this is more of a question or a feature request.
So is there a way to adjust blade height?
In my yard there are places that I would like blade to be lower and places where it should not be as low or it might hit something
Also this would be a great feature combined with other feature requests, while having different patterns in place one could make all kinds of nice patterns like on a football fields.
[Pic for reference](https://www.istockphoto.com/fi/vektori/jalkapallokentt%C3%A4-jalkapallokentt%C3%A4-ruohonleikkuu-kuviot-gm544356192-97829765l)

docgalaxyblock, 2022-08-31:
Unfortunate the YardForce mowers have not way to automatically adjust the height cause they use a big thread around the mowing motor chassi part there manual adjustment is mandatory

*maybe in the future of the project some crazy 3d printing people develop a solution - maybe*

Closed 2023-06-28.

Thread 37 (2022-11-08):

[0.10.x] WT901 pad is too narrow for manual soldering

rfvermut, 2022-11-08:

Closed 2022-12-05.

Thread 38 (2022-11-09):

[0.10.x] PRi socket needs to be taller

rfvermut, 2022-11-09:
Need to find one to match the distancers (12mm)

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

rfvermut, 2022-12-05:
https://www.lcsc.com/product-detail/_Liansheng-_C2685119.html is a good answer but it has protruding pins at the bottom to fix the part. Need to update footprint/PCB.

Closed 2022-12-23.

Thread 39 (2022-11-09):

Gardena Mower Compatibility

JasperMC, 2022-11-09:
Hi fellow robot mower owners,

I was wondering if anyone has tried converting a Gardena mower with this project.

Some Gardena mowers have a slot for a smart module, and I am wondering if that could be a way into controlling it without replacing hardware.

samborambo, 2023-04-03:
I have a Gardena Minimo 500. First thing I did was pull it apart to see how easy it would be to modify for OpenMower.

The motor controllers, charging system, STM32 microcontroller and bluetooth are on one conformally coated main board with the charging terminals mounted on it. Test pads and prog pins are exposed. I clean replacement would be to also replace the charging terminals with a 3D printed piece and some copper sheet.

All motors are brushless DC with integrated hall sensors, by the looks of it. Plenty of space inside around the main board. Nominal 18V system.

There's an RJ45 flat cable to another module at the rear, containing a USB-B connector that is accessible externally from a rubber plug. I haven't probed it yet. I'm guessing that the inductive sensor is also in this module.

That's pretty much all there is to the board. I'm just about finished setting up my perimeter wire. I'll probably start planning a mod and report back once it's working in normal operation first.

How well do DGPS sensors work under a thin plastic shell?

Sam.

patrickjsimons, 2023-04-03:
I've got two from the Sileno range, both of which have different boards and sensor arrangements. The main board in the 1600 older model gets really hot and the screen won't come on, so it looks like something on the board has short circuited internal, so it's time to take the OpenMower approach.

My first task is to modify one of the PCB designs in this repository to fit the OEM slot.

Someone mentioned on Discord that this is quite easy to do.

mikechristiansen, 2023-04-03:
Hi Patrick,
I might be involved in the chat on discord. I have 2 dead Husqvarna Automower 105 and a 305 which share the same PCB. I want to re layout the pcb to make it fit in my mower but have never used pcb design software and have a few other commitments at the moment so not too much time to learn. I do wonder if your mower shares a similar pcb? I know Gardena, Husqvarna and maybe others share some tech. I'll try and draw up the footprint and some photos of my pcb.
I do wonder if we can cloudfund someone to do the pcb layout work.
Thanks

patrickjsimons, 2023-04-03:
Hi Mike, When you say dead, is it battery related or do they both just not turn on?  I think after about three years these mowers have reach their life expectancy, whether it's motors, sensors or main board.  There is just no proper way too productively troubleshoot the main circuits, hence the reason I'm reluctant to just replace it with the OEM electronics.  I'm happy enough the way it chaotically approaches a lawn, as it's doing the job very well, so I'm more interested in being able to pinpoint issues and replace components. I'm also interested in moving away from the proprietary charging station as one of these has already been replaced under warranty.  I'll explore the option to resize the PCB and let you know how this pans out. In my case, it's probably more about stretching the real estate so it can be mounted, as opposed to reorganising the components.  Join the chat under Discord #open-mower-hardware

Closed 2023-06-28.

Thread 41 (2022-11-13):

3D gps holders holes are smaller than provided nuts

rfvermut, 2022-11-13:

rfvermut, 2023-02-13:
reinforced with din912 M2 x 20mm screws

rfvermut, 2023-02-15:
https://www.printables.com/model/399477-openmower-gps-mount-for-yardforce-classic-500-rev2

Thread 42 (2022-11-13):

Charger PCB - add missing parts to the kit, rethink the assembly process

rfvermut, 2022-11-13:
Are we supposed to remove the 4-pole terminal and resolder it to the PCB? or duplicate them?..

rfvermut, 2023-02-13:
0.11 kit includes extra terminals and alternative connectors

Closed 2023-02-13.

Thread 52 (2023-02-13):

Deprecate speaker in favor of buzzer

rfvermut, 2023-02-13:

rfvermut, 2023-02-13:
3d parts for ref https://www.printables.com/de/model/290760-openmower-wifi-dongle-speaker-holder-yardforce-cla

rfvermut, 2023-02-26:
Resolved by https://github.com/ClemensElflein/OpenMower/pull/54

Closed 2023-03-03.

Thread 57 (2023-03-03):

rain sensor always powered

rfvermut, 2023-03-03:
rain sensor always powered? IIUC on most mowers just power it and measure resistance every few minutes to reduce corrosion

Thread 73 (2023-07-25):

Work with bad WiFi coverage ?

JBaptisme33, 2023-07-25:
Hi,

Thanls for hard work. Mower work, and Vermut kit permit a fast mounting scenario :)
Is there a way to provide a working mode with a low / bad wifi garden coverage ?
Indeed, in some place, WiFi coverage is ok, but in many another, coverage is pretty bad / nonworking.
Can we imagine a "best effort" mode with no rtk correction ? (RTK correction should be re-done when mower re-enter into wifi covered zone)

Regards

ClemensElflein, 2024-03-10:
Currently, the software will continue for some time after losing WIFI (and therefore RTK fix). The issue is that accuracy is so low that it might crash into stuff or exit the lawn entirely when it is close to obstacles or the lawn boundary.

I kind of like the idea though, since in theory we could implement something like "if no RTK fix, don't drive closer than 2m to a lawn boundary or obstacle", which will allow the mower to continue in "safe" areas.

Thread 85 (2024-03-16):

Improving the ADC

sraillard, 2024-03-16:
The low level code, running on RPI Pico, is reading 3 analog values:
- Battery voltage
- Power voltage
- Battery charging current

The ADC seems to be noisy, using a moving average on 10 samples should improve the stability of the measures.

Also, I would be great if ratio can be configured (using UART commands) so calibration can be done for these 3 values (right now, the ratio are fixed in code, and I can observe a noticeable difference in voltage reading, this is especially important for monitoring the battery voltage).

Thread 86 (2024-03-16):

Voltage drop during charging and charger improvements

sraillard, 2024-03-16:
The documentation recommend to set to 29.2v the voltage of the docking station.

When charging, the current is going through:
- D3 and D2 diodes
- R51 shunt
- Q6 mosfet

The total voltage drop is around 0.7v, meaning that the battery can only get 28.5v (so it can't  be fully charged).
Also, in the low level code, the charging is enabled until the battery reach 29v (that is impossible), so the battery is in float charging, something not optimal for Li-ion batteries.

Most of the voltage drop are in D3, D2 and Q6. The shunt value can be increased to improve its precision, for example with a value of 0.01R or 0.02R (the voltage will still be negligible).

A better way to manage the charging could be increasing the docking station voltage, then detecting when the charging current is under 50mA, disabling the charging until the battery voltage drop like 0.5v.

houk001, 2024-07-06:
And that is ok.
Battery is 7 cell Li-Ion pack so 7 x 4.1V full charge cell  is 28.7V.   This is not LiPo battery where you have 4.2V full charge per cell
28.5 for battery extend his life for about year or two :D

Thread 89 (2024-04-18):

Remove copper below CC/CV module on Dock PCB

ClemensElflein, 2024-04-18:
Since the red PCB for the dock does not feature standoffs anymore, we should remove the copper below the CC/CV module.

If people screw the module so hard that they damage the silkscreen, there might be shorts.

houk001, 2024-07-04:
Or just add spacers about 2 milimeter high to separate CC/CV module from board. I create spacers from heat shrink tube because also worried about shorts.

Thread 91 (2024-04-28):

Last main board pinout

roque-canales, 2024-04-28:
Hello, i just ordered last mainboard, and i plan to install it in my old l200e robot mower (3 brushless motor) and i need the pinout of the last openmower mainboard to install it. Also i need to tune the esc with vesc software so in need to know where to connect the usb to set the vesc software ( are the vesc foc included foc capable or only bdlc?)
Thank you

ClemensElflein, 2024-05-02:
Schematic of the Mainboard is hosted here: https://clemenselflein.github.io/OpenMower/

The ESCs have both FOC and BLDC support.

Closed 2024-05-02.

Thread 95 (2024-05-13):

Test for and fix overvoltage conditions

ClemensElflein, 2024-05-13:
when the mower is fully charged and the mowing motor breaks, the induced voltage spike might be too high.

- we need to verify that this is happening
- if it is happening, we need to protect against it

quelqundev, 2024-05-13:
Hi ! I would recommend to never charge the battery at full charge to be able to absord current rejection. Is it possible to configure a max charge voltage ?

Furthermore i belive it is better to avoid little cycle charge at high % (i mean it "costs" more cycle charge to do 20%=>50% than 70%=>100%). Maybe adding a max charge at 80% would allow to improve the battery longevity ?

I'm trying to help, thanks for your great job guys !! 👍

ClemensElflein, 2024-05-13:
you can set the max charge voltage to whatever you like, what do you mean it "costs" more to charge the last 30% than other 30%?

anyways the original issue is still relevant for people who decide to charge the battery to 100%

quelqundev, 2024-05-13:
I recommend you to read this good article : https://accubattery.zendesk.com/hc/en-us/articles/210224725-Charging-research-and-methodology

The more important principle about Lithium battery is to stop charging before the "constant phase".
Thus i consider it is to you to find a balance between charging at full capacith but "degrading" battery capacity faster...or charging at 80% but preserving battery capacity for longer time. 🔋

It's like a bonus that allow you to solve the hypothetic case of current rejection. 😎

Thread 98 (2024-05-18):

Model 500B (via Aldi Discounter) uses _two_ lift hall sensors per wheel / different connectors

plewka, 2024-05-18:
Other stuff of the set was matching nicely. But Yardforce now uses a dual sensor at this model's wheels, it seems.
They are using a 4pin connector per wheel with about the same mechanical size as the old 3pin connector (higher density).
Both are Y-connected to one 8pin connector which even means there are different original UI boards when looking for spare parts, now.

They printed the connector pinout to the PCB at the wheel. If the connector locking-nose is directed downwards and
you're looking from cable to connector, the pinout is VCC-GND-HA1-HA2.

plewka, 2024-05-19:
I started with first sensor, but that one is much too sensitive. I'm now using HA2, which is ok.

plewka, 2024-05-22:
At Discord Vermut explained how to simply plug the 3pin connector to the 4pin socket without issues.

Closed 2024-05-22.

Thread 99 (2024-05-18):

Model 500B (via Aldi Discounter) UI-Board should match better if switches are shifted by about 0.5mm

plewka, 2024-05-18:
This is a mechanical tolerance issue only. So maybe only keep this as a reminder if someone else notices this, too.

The rounded PCB is about 0.5mm too near to the cover of the rain sensor in wheel-to-wheel axis.
This is for feedback only. I had to use a Dremel to remove some plastics (~1mm) from that side of the rain
sensor cover.

This is probably connected to another minor issue:
I didn't put the rubber to the board and mount it but found it much easier to put the rubber in place at the cover
and place the PCB to its position from top.
Maybe this is caused by the fixing holes and the grit of the buttons, which are shifted 0.5mm at my mechanics, too.
The holes are big enough to tolerate this with some stress to the buttons, but one can see the holes not matching
perfectly before putting in the screws.

For my mechanics, the buttons should be moved towards the side of the rain sensor drain in wheel to wheel axis to
solve both issues. For an updated PCB - to keep it universal -, the rounded area could get a stronger cut and the holes again
could be bigger or oval hole.

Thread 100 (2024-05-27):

Q6 needs a voltage divider on the gate

ClemensElflein, 2024-05-27:
Currently Vgs is -30V on Q6 when the battery is fully charged, but the FET is only allowed up to -20V, we need to add a voltage divider

sisteck-sassuolo, 2024-07-02:
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

Is correct ?

ClemensElflein, 2024-07-02:
yes, that should do it. you can PR that change, if you like!

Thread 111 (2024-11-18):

stereo vision based lawn mower

maazmb, 2024-11-18:
Hello Clemens, your work and effort are indeed impressive. im curious if you ever thought aboiut implementing a stereo cam+imu+wheel encoders based localization rather than RTK (much more expensive)? If so, which front end detection algorithm would you suggest (feature detectors, photometric image gradient based or hybrid etc.)? Many Thanks :)

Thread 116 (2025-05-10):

Tab mower

Tigger86, 2025-05-10:
I recently joined here. I’ve recently gotten a robotic lawn mower from the brand TAB. Unfortunately, it’s not updateable… even though it has a USB port. I had the idea that maybe it would be possible to flash new firmware onto it. That’s how I came across this site. What do I need to find out to know if the robot can support this? I got a refund from Amazon for the robot. This is the one I’m talking about:

[](Rasenmäher Roboter Mähroboter -... https://www.amazon.de/dp/B0F4CPC56K?ref=ppx_pop_mob_ap_share)

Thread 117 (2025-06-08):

Possibility LIDAR sensor?

tirithen, 2025-06-08:
This is a super cool project. Might be interested of the version 2. But still I'm wondering about obstacle avoidance to deviate from the path if there are toys or people on the lawn during the run. There are LIDAR sensors for around €90 or so  https://www.amazon.se/-/en/youyeetoo-FHL-LD19-Lidar-Sensor-Resistant/dp/B0B1QCV4XR/262-5451151-7989726?psc=1 .

The description do mention ROS/ROS2 and raspberry pi. I wonder if something like that might be an option. No clue if it is weather resistant over time or not.

Either way, keep up your cool work, and keen to see more on the version 2 announcement.

barateau, 2025-08-27:
Hey hey, I have followed your wonderful project quite some time and have been dreaming of you mod for my yardforce OEM model. Anyway i did watch an interesting talk with greatscott and he highlighted some new IC thats high frequency radar.  Basically 57-64GHz  radar sensor with great visibility, this might be the actual game changer compared to the bumpers or even lidar that I feel even fail in a home environment.

Please have a look and say what you think about the functionality, as I sould say it could perhaps be a really good upgrade for version V2.5

https://www.ti.com/product/IWRL6432

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

barateau, 2025-08-27:
Did add a Q to greatscott, if he can give some insight on how to implement or leverage. Not only on the PCB but it would need a logic or trained LLM model to interpret the radar senor.

https://youtube.com/watch?v=D86an4uN7FE&lc=UgxEqrR4quBw1_4g5lF4AaABAg&feature=shared

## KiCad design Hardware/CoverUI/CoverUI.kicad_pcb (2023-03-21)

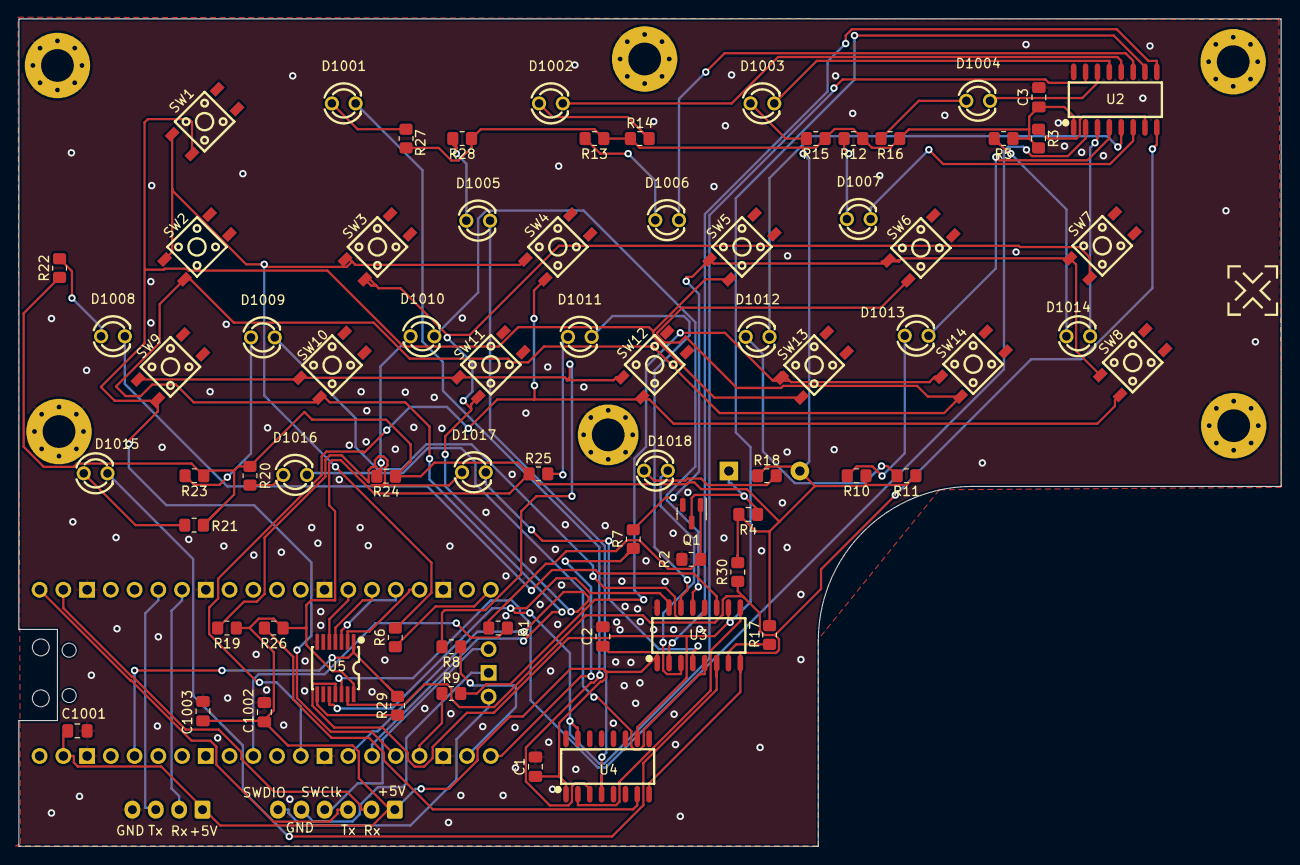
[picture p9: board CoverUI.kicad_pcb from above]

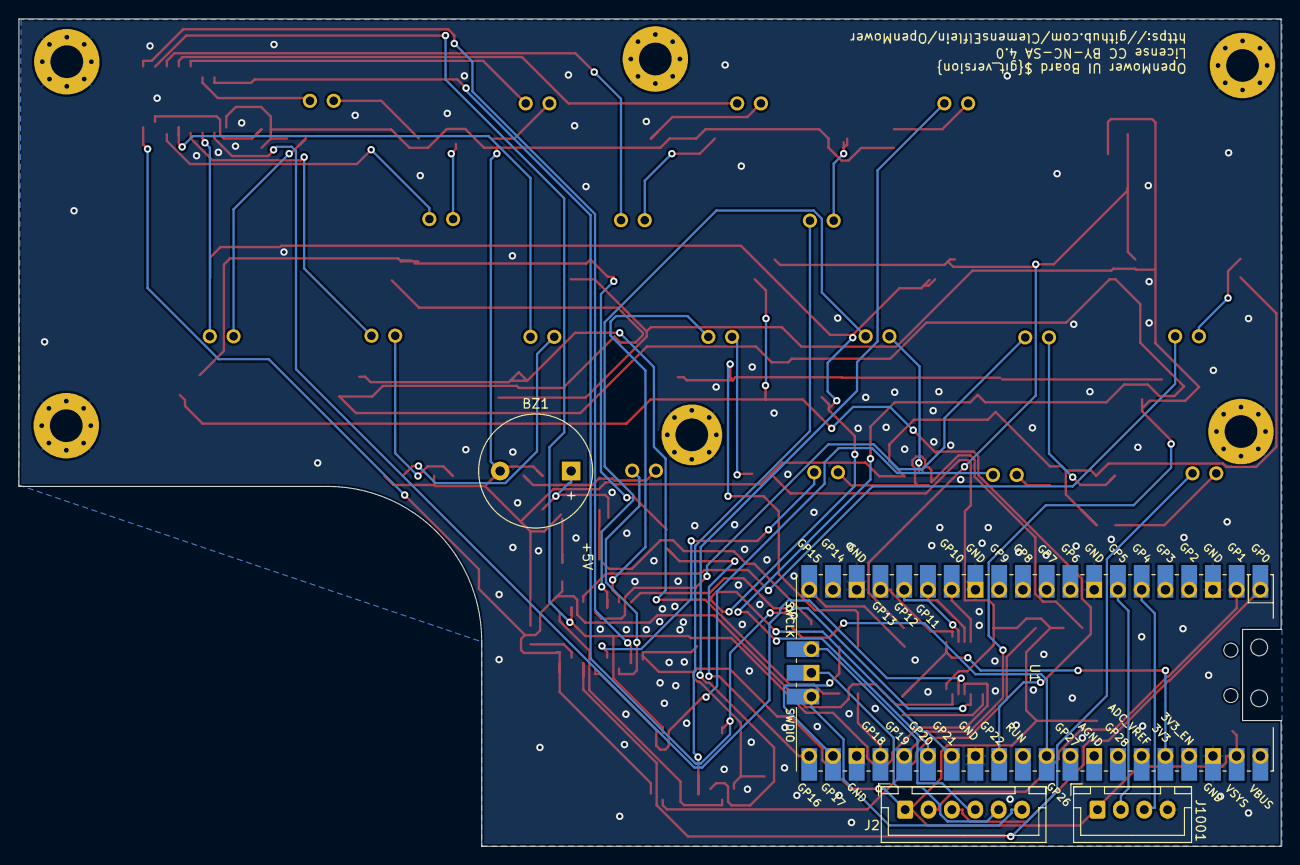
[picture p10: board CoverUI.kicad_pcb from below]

Board: 2 copper layers, 135.0 x 88.5 mm, 102 parts (4 on the bottom side), 75 nets.

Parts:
BZ1: Buzzer; Buzzer_12x9.5RM7.6
C1, C2, C3, C1001, C1002: 100nF; C_0805_2012Metric_Pad1.18x1.45mm_HandSolder
C1003: 1uF; C_0805_2012Metric_Pad1.18x1.45mm_HandSolder
D1001, D1002, D1003, D1004, D1005, D1006, D1007, D1008, D1009, D1010, D1011, D1012, D1013, D1014, D1015, D1016, D1017, D1018: 20mA 2V, Red; LED-TH_BD3.0-P2.54-FD
H1001, H1002, H1003, H1004, H1005, H1006: MountingHole_Pad; MountingHole_3.5mm_Pad_Via
J2: Conn_01x06_Male; JST_XH_B6B-XH-A_1x06_P2.50mm_Vertical
J1001: Conn_01x04_Male; JST_XH_B4B-XH-A_1x04_P2.50mm_Vertical
Q1: BSS138; SOT-23
R1, R4: 1k; R_0805_2012Metric_Pad1.20x1.40mm_HandSolder
R2: 47k; R_0805_2012Metric_Pad1.20x1.40mm_HandSolder
R3, R6, R7, R8, R9, R17, R26, R29, R30: 10k; R_0805_2012Metric_Pad1.20x1.40mm_HandSolder
R5, R10, R11, R12, R13, R14, R15, R16, R18, R19, R20, R21, R22, R23, R24, R25, R27, R28: 150; R_0805_2012Metric_Pad1.20x1.40mm_HandSolder
SP01, SP02, SP03, SP04, SP05, SP06, SP07, SP08, SP09, SP10, SP11, SP12, SP13, SP14, SP15, SP16: LedSpacer; LED_SPACER_3mm
SP17, SP18, SP20: LED_SPACER_3mm
SW1, SW2, SW3, SW4, SW5, SW6, SW7, SW8, SW9, SW10, SW11, SW12, SW13, SW14: SW_MEC_5G; SW-SMD_4P-L4.5-W4.5-P3.00-LS7.0
U1: Raspberry-Pico; RPi_Pico_SMD_TH
U2, U3, U4: TPIC6C596DRG4; SOIC-16_L10.8-W4.5-P1.27-LS6.8-BL
U5: RS0104YQ; TSSOP-14_L5.0-W4.4-P0.65-LS6.4-BL

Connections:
+3.3V: R29.2, U1.36 (3V3), U5.1 (VCCA)
+5V: BZ1.2 (+), C1.1, C2.1, C3.1, C1001.1, C1002.1, C1003.1, J2.1, J1001.1, R3.1, R4.2, R5.1, R10.1, R11.1, R12.1, R13.1, R14.1, R15.1, R16.1, R17.1, R18.1, R19.1, R20.1, R21.1, R22.1, R23.1, R24.1, R25.1, R26.1, R27.1, R28.1, R30.2, U1.39 (VSYS), U2.1 (VCC), U3.1 (VCC), U4.1 (VCC), U5.14 (VCCB)
/LEDmux/G: R30.1, U2.8 (~G), U3.8 (~G), U4.8 (~G), U5.13 (B1)
/LEDmux/G_3.3V: U1.17 (GPIO13), U5.2 (A1)
/LEDmux/RCK: U2.10 (RCK), U3.10 (RCK), U4.10 (RCK), U5.11 (B3)
/LEDmux/RCK_3.3V: U1.15 (GPIO11), U5.4 (A3)
/LEDmux/SER: U2.2 (SER/IN), U5.12 (B2)
/LEDmux/SER_3.3V: U1.16 (GPIO12), U5.3 (A2)
/LEDmux/SRCK: U2.15 (SRCK), U3.15 (SRCK), U4.15 (SRCK), U5.10 (B4)
/LEDmux/SRCK_3.3V: U1.14 (GPIO10), U5.5 (A4)
/RaspberryPico/GP15: R6.1, U1.20 (GPIO15)
/RaspberryPico/GP16: R7.1, U1.21 (GPIO16)
/RaspberryPico/GP17: R8.1, U1.22 (GPIO17)
/RaspberryPico/GP18: R9.1, U1.24 (GPIO18)
/RaspberryPico/GP19: SW1.3 (B), SW5.3 (B), SW9.3 (B), SW13.3 (B), U1.25 (GPIO19)
/RaspberryPico/GP20: SW2.3 (B), SW6.3 (B), SW10.3 (B), SW14.3 (B), U1.26 (GPIO20)
/RaspberryPico/GP21: SW3.3 (B), SW7.3 (B), SW11.3 (B), U1.27 (GPIO21)
/RaspberryPico/GP22: SW4.3 (B), SW8.3 (B), SW12.3 (B), U1.29 (GPIO22)
/RaspberryPico/GP26: R1.1, U1.31 (GPIO26_ADC0)
/RaspberryPico/PiCo_RX: J1001.2, U1.7 (GPIO5)
/RaspberryPico/PiCo_TX: J1001.3, U1.6 (GPIO4)
GND: C1.2, C2.2, C3.2, C1001.2, C1002.2, C1003.2, H1001.1, H1002.1, H1003.1, H1004.1, H1005.1, H1006.1, J1001.4, Q1.2 (S), R2.2, U1.3 (GND), U1.8 (GND), U1.13 (GND), U1.18 (GND), U1.23 (GND), U1.28 (GND), U1.38 (GND), U2.16 (GND), U3.16 (GND), U4.16 (GND), U5.7 (GND)
unnamed: BZ1.1 (-), Q1.3 (D), R4.1
unnamed: D1001.1 (A), R27.2
unnamed: D1001.2 (K), U4.3 (DRAIN0)
unnamed: D1002.1 (A), R14.2
unnamed: D1002.2 (K), U2.12 (DRAIN5)
unnamed: D1003.1 (A), R15.2
unnamed: D1003.2 (K), U2.13 (DRAIN6)
unnamed: D1004.1 (A), R16.2
unnamed: D1004.2 (K), U2.14 (DRAIN7)
unnamed: D1005.1 (A), R28.2
unnamed: D1005.2 (K), U4.4 (DRAIN1)
unnamed: D1006.1 (A), R13.2
unnamed: D1006.2 (K), U2.11 (DRAIN4)
unnamed: D1007.1 (A), R12.2
unnamed: D1007.2 (K), U2.6 (DRAIN3)
unnamed: D1008.1 (A), R22.2
unnamed: D1008.2 (K), U3.11 (DRAIN4)
unnamed: D1009.1 (A), R23.2
unnamed: D1009.2 (K), U3.12 (DRAIN5)
unnamed: D1010.1 (A), R24.2
unnamed: D1010.2 (K), U3.13 (DRAIN6)
unnamed: D1011.1 (A), R25.2
unnamed: D1011.2 (K), U3.14 (DRAIN7)
unnamed: D1012.1 (A), R11.2
unnamed: D1012.2 (K), U2.5 (DRAIN2)
unnamed: D1013.1 (A), R10.2
unnamed: D1013.2 (K), U2.4 (DRAIN1)
unnamed: D1014.1 (A), R5.2
unnamed: D1014.2 (K), U2.3 (DRAIN0)
unnamed: D1015.1 (A), R21.2
unnamed: D1015.2 (K), U3.6 (DRAIN3)
unnamed: D1016.1 (A), R20.2
unnamed: D1016.2 (K), U3.5 (DRAIN2)
unnamed: D1017.1 (A), R19.2
unnamed: D1017.2 (K), U3.4 (DRAIN1)
unnamed: D1018.1 (A), R18.2
unnamed: D1018.2 (K), U3.3 (DRAIN0)
unnamed: J2.2, U1.2 (GPIO1)
unnamed: J2.3, U1.1 (GPIO0)
unnamed: J2.4, U1.41 (SWCLK)
unnamed: J2.5, U1.42 (GND)
unnamed: J2.6, U1.43 (SWDIO)
unnamed: Q1.1 (G), R1.2, R2.1
unnamed: R3.2, U2.7 (~CLR)
unnamed: R6.2, SW1.1 (A), SW2.1 (A), SW3.1 (A), SW4.1 (A)
unnamed: R7.2, SW5.1 (A), SW6.1 (A), SW7.1 (A), SW8.1 (A)
unnamed: R8.2, SW9.1 (A), SW10.1 (A), SW11.1 (A), SW12.1 (A)
unnamed: R9.2, SW13.1 (A), SW14.1 (A)
unnamed: R17.2, U3.7 (~CLR)
unnamed: R26.2, U4.7 (~CLR)
unnamed: R29.1, U5.8 (OE)
unnamed: U2.9 (SER/OUT), U3.2 (SER/IN)
unnamed: U3.9 (SER/OUT), U4.2 (SER/IN)

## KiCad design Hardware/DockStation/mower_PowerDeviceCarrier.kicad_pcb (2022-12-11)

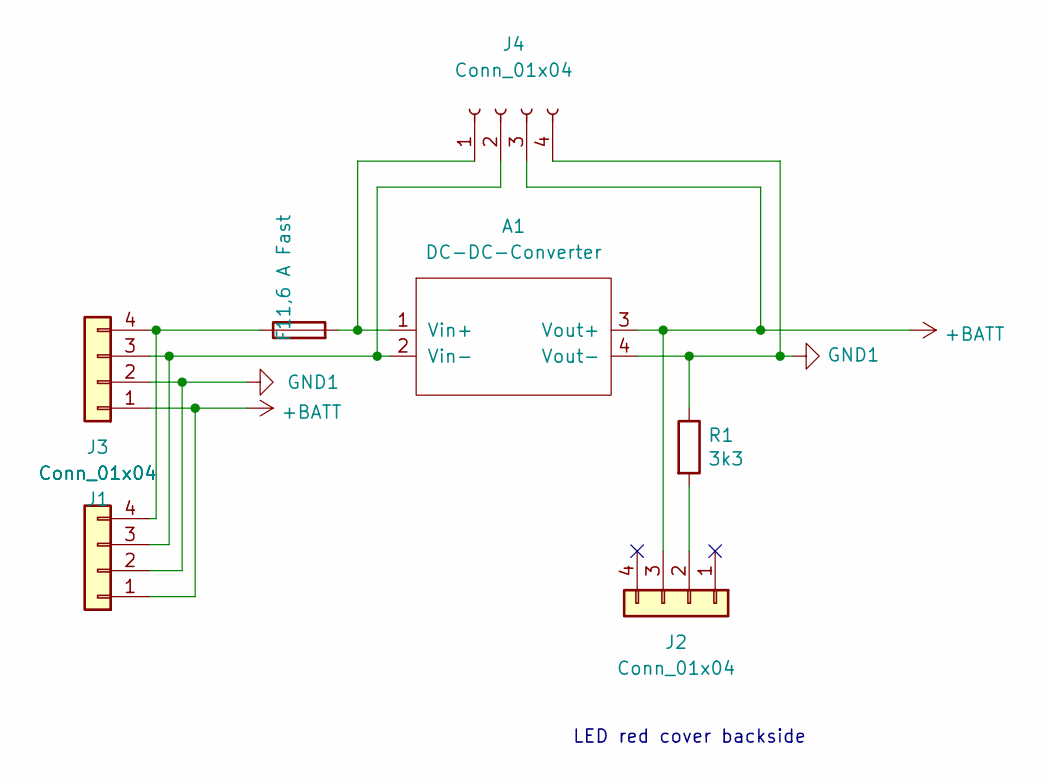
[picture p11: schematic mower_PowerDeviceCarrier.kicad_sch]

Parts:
A1: DC-DC-Converter; DC-DC-XL4016
F1: 1,6 A Fast; Fuseholder5x20_horiz_open_inline_Type-I
J1: Conn_01x04; PhoenixContact_MSTBVA_2,5_4-G-5,08_1x04_P5.08mm_Vertical
J2: Conn_01x04; PinHeader_1x04_P2.54mm_Horizontal
J3: Conn_01x04; PhoenixContact_MCV_1,5_4-G-3.81_1x04_P3.81mm_Vertical
J4: Conn_01x04; PinHeader_1x07_P2.54mm_Vertical
R1: 3k3; R_Axial_DIN0414_L11.9mm_D4.5mm_P15.24mm_Horizontal

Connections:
+BATT: A1.3 (Vout+), J1.1, J2.3, J3.1, J4.3
GND1: A1.4 (Vout-), J1.2, J3.2, J4.4, R1.1
unnamed: A1.1 (Vin+), F1.2, J4.1
unnamed: A1.2 (Vin-), J1.3, J3.3, J4.2
unnamed: F1.1, J1.4, J3.4
unnamed: J2.2, R1.2

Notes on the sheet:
LED red cover backside

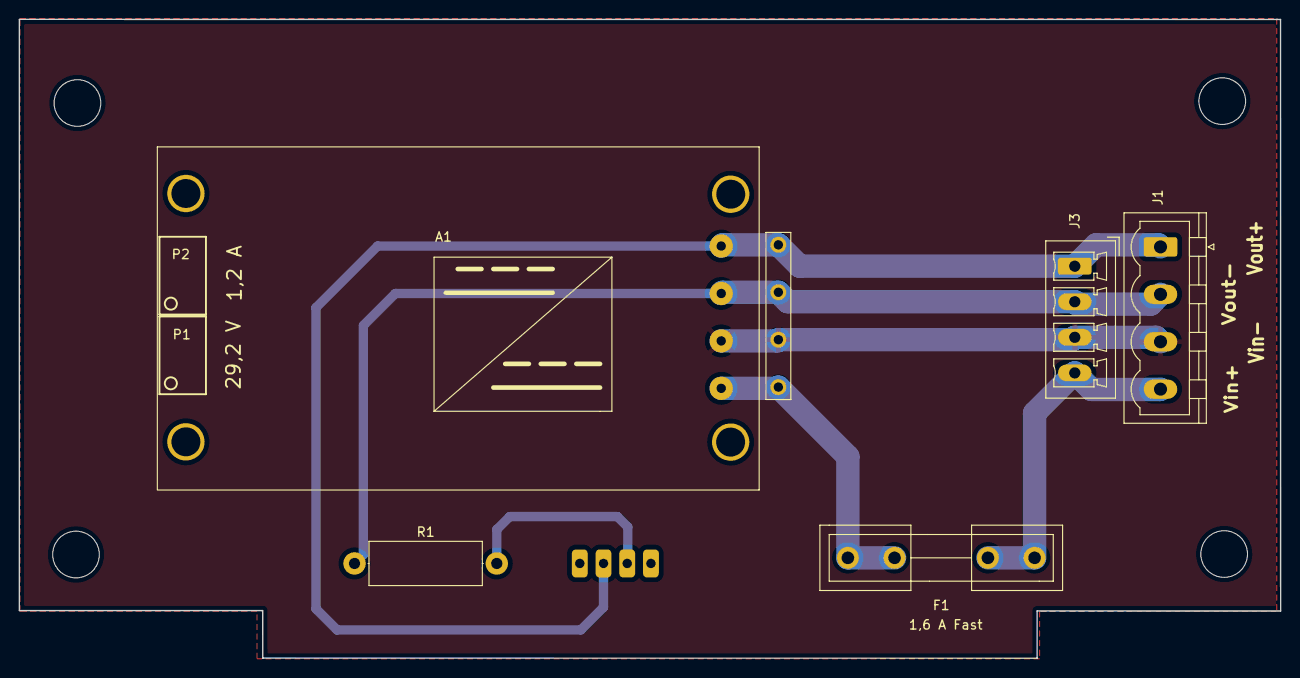
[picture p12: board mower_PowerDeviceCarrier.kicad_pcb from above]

Board: 2 copper layers, 135.1 x 68.4 mm, 7 parts (1 on the bottom side), 6 nets.

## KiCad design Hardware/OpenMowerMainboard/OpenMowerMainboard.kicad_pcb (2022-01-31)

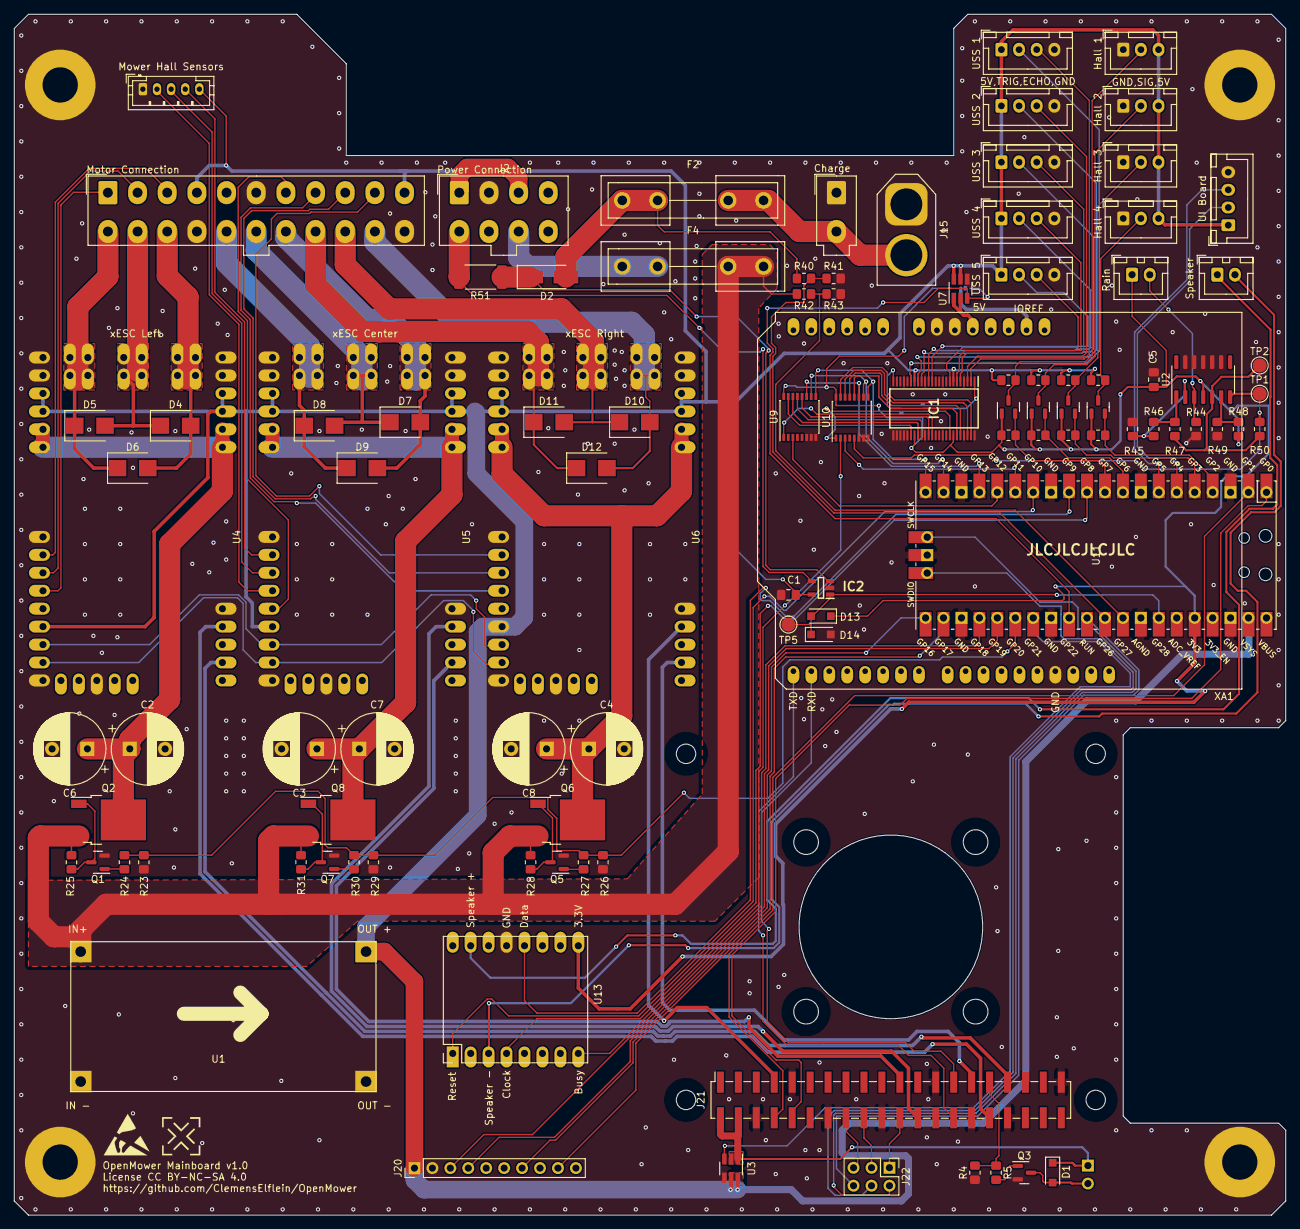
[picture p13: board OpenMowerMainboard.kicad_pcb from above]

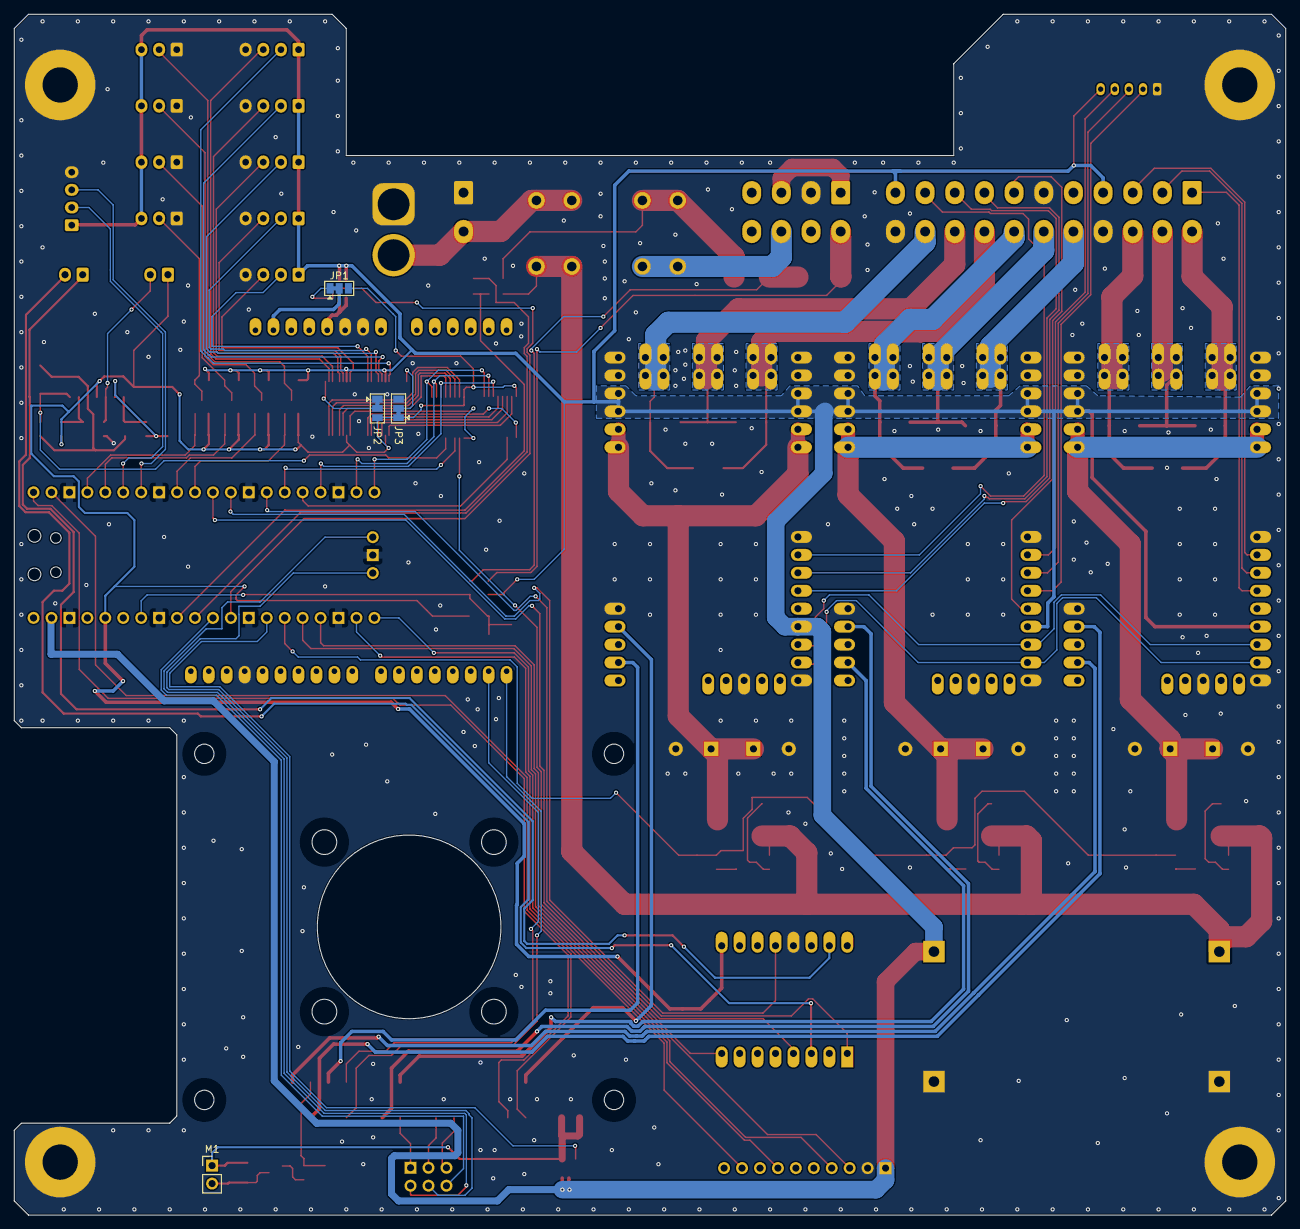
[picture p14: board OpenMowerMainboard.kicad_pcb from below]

Board: 2 copper layers, 180.0 x 170.0 mm, 110 parts (4 on the bottom side), 121 nets.

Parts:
C1, C5: 100n; C_0805_2012Metric_Pad1.18x1.45mm_HandSolder
C2, C3, C4, C6, C7, C8: C_Polarized; CP_Radial_D10.0mm_P5.00mm
D1, D13: D_Schottky; D_SOD-123F
D2: D_Schottky; D_SMA_Handsoldering
D4, D5, D6, D7, D8, D9, D10, D11, D12: D_TVS; D_SMB
D14: D_Zener; D_SOD-123F
F2, F4: Fuse; Fuseholder5x20_horiz_open_inline_Type-I
H1, H2, H3, H4: MountingHole_Pad; MountingHole_5mm_Pad
IC1: 74ALVC164245DGG,11; SOP50P810X120-48N
IC2: TSC101CILT; SOT95P280X145-5N
J1: Conn_02x11_Top_Bottom; Molex_Mini-Fit_Jr_5566-22A_2x11_P4.20mm_Vertical
J2: Conn_02x04_Top_Bottom; Molex_Mini-Fit_Jr_5566-08A_2x04_P4.20mm_Vertical
J3: Conn_01x02; Molex_Mini-Fit_Jr_5566-02A_2x01_P4.20mm_Vertical
J5, J6, J7, J8, J9, J19: Conn_01x04; JST_XH_B4B-XH-A_1x04_P2.50mm_Vertical
J10: Conn_01x05; JST_PH_B5B-PH-K_1x05_P2.00mm_Vertical
J11, J12, J13, J14: Conn_01x03_Male; JST_XH_B3B-XH-A_1x03_P2.50mm_Vertical
J15: Conn_01x02_Male; AMASS_XT60-M_1x02_P7.20mm_Vertical
J17, J18: Conn_01x02; JST_XH_B2B-XH-A_1x02_P2.50mm_Vertical
J20: Conn_01x10_Female; PinHeader_1x10_P2.54mm_Vertical
J21: Raspberry_Pi_2_3; PinSocket_2x20_P2.54mm_Vertical_SMD
J22: Conn_02x03_Odd_Even; PinHeader_2x03_P2.54mm_Vertical
JP1, JP2, JP3: SolderJumper_3_Bridged12; SolderJumper-3_P1.3mm_Bridged12_Pad1.0x1.5mm
M1: Fan; PinHeader_1x02_P2.54mm_Vertical
Q1, Q3, Q5, Q7, Q13, Q14, Q15, Q16: BSS138; SOT-23
Q2, Q6, Q8: Q_PMOS_GDS; TO-252-2
R3, R4, R5, R6, R9, R10, R15, R16, R19, R20, R23, R24, R25, R26, R27, R28, R29, R30, R31, R40, R41, R42, R43: R; R_0805_2012Metric_Pad1.20x1.40mm_HandSolder
R44, R46: 47k; R_0805_2012Metric_Pad1.20x1.40mm_HandSolder
R45: 1k; R_0805_2012Metric_Pad1.20x1.40mm_HandSolder
R47: 560; R_0805_2012Metric_Pad1.20x1.40mm_HandSolder
R48, R50: 10k; R_0805_2012Metric_Pad1.20x1.40mm_HandSolder
R49: 6.8k; R_0805_2012Metric_Pad1.20x1.40mm_HandSolder
R51: R; R_2512_6332Metric_Pad1.40x3.35mm_HandSolder
TP1, TP2, TP5: TestPoint; TestPoint_Pad_D2.0mm
U1: LM2596S_MODULE
U2: MCP604; SOIC-14_3.9x8.7mm_P1.27mm
U3, U7: SIP32509DT; SOT-23-6_Handsoldering
U4, U5, U6: xESC2
U9, U10: 74HC4051; SSOP-16_4.4x5.2mm_P0.65mm
U11: Pico; RPi_Pico_SMD_TH
U13: WTV020
XA1: Arduino_Uno_Shield

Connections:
+3V3: C5.2, D13.1 (K), IC1.31 (VCC(A)_1), IC1.42 (VCC(A)_2), J17.1, JP1.3 (B), JP2.3 (B), JP3.1 (A), Q13.1 (G), Q14.1 (G), Q15.1 (G), Q16.1 (G), R3.1, R9.1, R15.1, R19.1, R48.2, U2.4 (V+), U9.16 (VCC), U10.16 (VCC), U11.36 (3V3), U13.16 (VIN)
+5V: C1.1, IC1.7 (VCC(B)_1), IC1.18 (VCC(B)_2), IC2.5 (VCC), J1.4, J1.11, J5.1, J6.1, J7.1, J8.1, J9.1, J10.5, J11.3, J12.3, J13.3, J14.3, J19.1, J20.1, R6.1, R10.1, R16.1, R20.1, U1.3 (OUT+), U3.5 (VIN), U3.6 (VIN), U4.5V, U5.5V, U6.5V, U7.5 (VIN), U7.6 (VIN), U11.39 (VSYS)
/CHARGE_CURRENT: D13.2 (A), D14.1 (K), IC2.1 (OUT), TP5.1, U11.34 (GPIO28_ADC2)
/ESCs/MC_HALL_U: J10.2, U5.4 (HALL_U)
/ESCs/MC_HALL_V: J10.3, U5.5 (HALL_V)
/ESCs/MC_HALL_W: J10.4, U5.6 (HALL_W)
/ESCs/MC_PHASE_U: D7.2 (A2), D9.2 (A2), J1.18, U5.U
/ESCs/MC_PHASE_V: D7.1 (A1), D8.2 (A2), J1.17, U5.V
/ESCs/MC_PHASE_W: D8.1 (A1), D9.1 (A1), J1.16, U5.W
/ESCs/MC_POWER: R23.1, R24.1, R26.1, R27.1, R29.1, R30.1, U11.26 (GPIO20)
/ESCs/MC_RX: J21.24 (~CE0/GPIO8), U5.14 (NCS/RX)
/ESCs/MC_TEMP: J1.7, U5.3 (TEMPERATURE)
/ESCs/MC_TX: J21.21 (MISO0/GPIO9), U5.12 (MOSI/TX)
/ESCs/ML_HALL_U: J1.1, U4.4 (HALL_U)
/ESCs/ML_HALL_V: J1.2, U4.5 (HALL_V)
/ESCs/ML_HALL_W: J1.3, U4.6 (HALL_W)
/ESCs/ML_PHASE_U: D4.2 (A2), D6.2 (A2), J1.14, U4.U
/ESCs/ML_PHASE_V: D4.1 (A1), D5.2 (A2), J1.13, U4.V
/ESCs/ML_PHASE_W: D5.1 (A1), D6.1 (A1), J1.12, U4.W
/ESCs/ML_RX: J21.32 (PWM0/GPIO12), U4.14 (NCS/RX)
/ESCs/ML_TX: J21.33 (PWM1/GPIO13), U4.12 (MOSI/TX)
/ESCs/MOSFET_SWITCH1/VOUT: C4.1, C8.1, Q6.2 (D), U6.VM (VIN)
/ESCs/MOSFET_SWITCH2/VOUT: C3.1, C7.1, Q8.2 (D), U5.VM (VIN)
/ESCs/MOSFET_SWITCH/VOUT: C2.1, C6.1, Q2.2 (D), U4.VM (VIN)
/ESCs/MR_HALL_U: J1.8, U6.4 (HALL_U)
/ESCs/MR_HALL_V: J1.9, U6.5 (HALL_V)
/ESCs/MR_HALL_W: J1.10, U6.6 (HALL_W)
/ESCs/MR_PHASE_U: D10.2 (A2), D12.2 (A2), J1.21, U6.U
/ESCs/MR_PHASE_V: D10.1 (A1), D11.2 (A2), J1.20, U6.V
/ESCs/MR_PHASE_W: D11.1 (A1), D12.1 (A1), J1.19, U6.W
/ESCs/MR_RX: J21.7 (GCLK0/GPIO4), U6.14 (NCS/RX)
/ESCs/MR_TX: J21.29 (GCLK1/GPIO5), U6.12 (MOSI/TX)
/GPS/GPS_POWER: U7.1 (VOUT), U7.2 (VOUT), XA1.5V1 (5V)
/GPS/POWER_EN: JP1.1 (A), U7.3 (ENABLE), U11.29 (GPIO22)
/GPS/RXD: J21.27 (ID_SD/GPIO0), XA1.D1 (D1_TX0)
/GPS/TXD: J21.28 (ID_SC/GPIO1), XA1.D0 (D0_RX0)
/IMU/MISO: J20.7, U11.21 (GPIO16)
/IMU/MOSI: J20.4, U11.25 (GPIO19)
/IMU/SCK: J20.3, U11.24 (GPIO18)
/IMU/~CS: J20.9, U11.22 (GPIO17)
/RAIN_DETECTED: R50.2, TP1.1, U2.7, U10.5 (A5)
/RaspberryPi/PICO_RESET: J22.6, U11.30 (RUN)
/RaspberryPi/PICO_SWCLK: J22.2, U11.41 (SWCLK)
/RaspberryPi/PICO_SWDIO: J22.4, U11.43 (SWDIO)
/RaspberryPi/POWER_EN: U3.3 (ENABLE), U11.27 (GPIO21)
/RaspberryPi/RASPI_FAN_ON: J21.31 (GCLK2/GPIO6), R4.2, R5.1
/RaspberryPi/RASPI_POWER: D1.1 (K), J21.2 (5V), J21.4 (5V), M1.1 (+), U3.1 (VOUT), U3.2 (VOUT)
/RaspberryPi/UART0_RXD: J21.10 (GPIO15/RXD), U11.1 (GPIO0)
/RaspberryPi/UART0_TXD: J21.8 (GPIO14/TXD), U11.2 (GPIO1)
/RobotConnectors/CHARGE_SHUNT_MINUS: IC2.4 (VM), J2.5, R51.2
/RobotConnectors/CHARGE_SHUNT_PLUS: D2.1 (K), IC2.3 (VP), R51.1
/RobotConnectors/HALL_SWITCH_1: Q13.2 (S), R3.2, U11.10 (GPIO7)
/RobotConnectors/HALL_SWITCH_1_5V: J11.2, Q13.3 (D), R6.2
/RobotConnectors/HALL_SWITCH_2: Q14.2 (S), R9.2, U11.9 (GPIO6)
/RobotConnectors/HALL_SWITCH_2_5V: J12.2, Q14.3 (D), R10.2
/RobotConnectors/HALL_SWITCH_3: Q15.2 (S), R15.2, U11.5 (GPIO3)
/RobotConnectors/HALL_SWITCH_3_5V: J13.2, Q15.3 (D), R16.2
/RobotConnectors/HALL_SWITCH_4: Q16.2 (S), R19.2, U11.4 (GPIO2)
/RobotConnectors/HALL_SWITCH_4_5V: J14.2, Q16.3 (D), R20.2
/RobotConnectors/LED_RX: J19.2, U11.6 (GPIO4)
/RobotConnectors/LED_TX: J19.3, U11.7 (GPIO5)
/RobotConnectors/RAIN-: J17.2, R44.2, U2.3 (+)
/RobotConnectors/SPEAKER_MINUS: J18.2, U13.5 (SPEAKER-)
/RobotConnectors/SPEAKER_PLUS: J18.1, U13.4 (SPEAKER+)
/RobotConnectors/USS_1_ECHO: IC1.47 (1A0), U10.15 (A2)
/RobotConnectors/USS_1_ECHO_5V: IC1.2 (1B0), J5.3
/RobotConnectors/USS_1_TRIGGER: IC1.30 (2A4), U9.15 (A2)
/RobotConnectors/USS_1_TRIGGER_5V: IC1.19 (2B4), J5.2
/RobotConnectors/USS_2_ECHO: IC1.46 (1A1), U10.14 (A1)
/RobotConnectors/USS_2_ECHO_5V: IC1.3 (1B1), J6.3
/RobotConnectors/USS_2_TRIGGER: IC1.32 (2A3), U9.14 (A1)
/RobotConnectors/USS_2_TRIGGER_5V: IC1.17 (2B3), J6.2
/RobotConnectors/USS_3_ECHO: IC1.44 (1A2), U10.13 (A0)
/RobotConnectors/USS_3_ECHO_5V: IC1.5 (1B2), J7.3
/RobotConnectors/USS_3_TRIGGER: IC1.33 (2A2), U9.13 (A0)
/RobotConnectors/USS_3_TRIGGER_5V: IC1.16 (2B2), J7.2
/RobotConnectors/USS_4_ECHO: IC1.43 (1A3), U10.12 (A3)
/RobotConnectors/USS_4_ECHO_5V: IC1.6 (1B3), J8.3
/RobotConnectors/USS_4_TRIGGER: IC1.35 (2A1), U9.12 (A3)
/RobotConnectors/USS_4_TRIGGER_5V: IC1.14 (2B1), J8.2
/RobotConnectors/USS_5_ECHO: IC1.41 (1A4), U10.1 (A4)
/RobotConnectors/USS_5_ECHO_5V: IC1.8 (1B4), J9.3
/RobotConnectors/USS_5_TRIGGER: IC1.36 (2A0), U9.1 (A4)
/RobotConnectors/USS_5_TRIGGER_5V: IC1.13 (2B0), J9.2
/RobotConnectors/V_CHARGE: D2.2 (A), F2.1, R40.2
/pico/MUX_ADDRESS_0: U9.11 (S0), U10.11 (S0), U11.17 (GPIO13)
/pico/MUX_ADDRESS_1: U9.10 (S1), U10.10 (S1), U11.19 (GPIO14)
/pico/MUX_ADDRESS_2: U9.9 (S2), U10.9 (S2), U11.20 (GPIO15)
/pico/MUX_INPUT: U10.3 (A), U11.15 (GPIO11)
/pico/MUX_OUTPUT: U9.3 (A), U11.16 (GPIO12)
/pico/SOUND_BUSY: U10.2 (A6), U13.15 (BUSY)
/pico/SOUND_CLK: U11.11 (GPIO8), U13.7 (CLK)
/pico/SOUND_DATA: U11.12 (GPIO9), U13.10 (Data)
/pico/SOUND_RESET: U11.14 (GPIO10), U13.1 (RESET)
/pico/V_CHARGE: R40.1, R41.2, U11.31 (GPIO26_ADC0)
/pico/V_IN: R42.1, R43.2, U11.32 (GPIO27_ADC1)
GND: C1.2, C2.2, C3.2, C4.2, C5.1, C6.2, C7.2, C8.2, D14.2 (A), H1.1, H2.1, H3.1, H4.1, IC1.4 (GND_1), IC1.10 (GND_2), IC1.15 (GND_3), IC1.21 (GND_4), IC1.25 (~2OE), IC1.26 (2A7), IC1.27 (2A6), IC1.28 (GND_5), IC1.29 (2A5), IC1.34 (GND_6), IC1.39 (GND_7), IC1.45 (GND_8), IC1.48 (~1OE), IC2.2 (GND), J1.6, J1.15, J1.22, J2.2, J3.1, J5.4, J6.4, J7.4, J8.4, J9.4, J10.1, J11.1, J12.1, J13.1, J14.1, J15.1, J19.4, J20.2, J21.6 (GND), J21.9 (GND), J21.14 (GND), J21.20 (GND), J21.25 (GND), J21.30 (GND), J21.34 (GND), J21.39 (GND), JP2.1 (A), JP3.3 (B), Q1.2 (S), Q3.2 (S), Q5.2 (S), Q7.2 (S), R4.1, R23.2, R26.2, R29.2, R41.1, R43.1, R44.1, R45.1, R49.2, U1.1 (IN-), U1.4 (OUT-), U2.9 (-), U2.10 (+), U2.11 (V-), U2.12 (+), U2.13 (-), U3.4 (GND), U4.GND, U5.GND, U6.GND, U7.4 (GND), U9.6 (~E), U9.7 (VEE), U9.8 (GND), U10.6 (~E), U10.7 (VEE), U10.8 (GND), U11.3 (GND), U11.8 (GND), U11.13 (GND), U11.18 (GND), U11.23 (GND), U11.28 (GND), U11.33 (AGND), U11.38 (GND), U11.42 (GND), U13.8 (GND), XA1.GND1 (GND), XA1.GND2 (GND), XA1.GND3 (GND)
unnamed: D1.2 (A), M1.2 (-), Q3.3 (D)
unnamed: F2.2, J3.2, J15.2
unnamed: F4.1, J2.7
unnamed: IC1.1 (1DIR), JP2.2 (C)
unnamed: IC1.24 (2DIR), JP3.2 (C)
unnamed: J2.1, J2.3
unnamed: J21.16 (GPIO23), J22.5
unnamed: J21.18 (GPIO24), J22.3
unnamed: J21.22 (GPIO25), J22.1
unnamed: JP1.2 (C), XA1.IORF (IOREF)
unnamed: Q1.1 (G), R24.2
unnamed: Q1.3 (D), Q2.1 (G), R25.2
unnamed: Q3.1 (G), R5.2
unnamed: Q5.1 (G), R27.2
unnamed: Q5.3 (D), Q6.1 (G), R28.2
unnamed: Q7.1 (G), R30.2
unnamed: Q7.3 (D), Q8.1 (G), R31.2
unnamed: R45.2, R46.2, U2.2 (-)
unnamed: R46.1, R47.1, U2.1
unnamed: R47.2, R50.1, TP2.1, U2.5 (+)
unnamed: R48.1, R49.1, U2.6 (-)
unnamed: U4.1 (CAN_L), U5.1 (CAN_L), U6.1 (CAN_L)
unnamed: U4.2 (CAN_H), U5.2 (CAN_H), U6.2 (CAN_H)
V_BATT: F4.2, Q2.3 (S), Q6.3 (S), Q8.3 (S), R25.1, R28.1, R31.1, R42.2, U1.2 (IN+)

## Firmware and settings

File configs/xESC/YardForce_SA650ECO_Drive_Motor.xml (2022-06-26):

<?xml version="1.0" encoding="UTF-8"?>
<MCConfiguration>
    <ConfigVersion>2</ConfigVersion>
    <pwm_mode>1</pwm_mode>
    <comm_mode>0</comm_mode>
    <motor_type>2</motor_type>
    <sensor_mode>0</sensor_mode>
    <l_current_max>6.51866</l_current_max>
    <l_current_min>-6.51866</l_current_min>
    <l_in_current_max>5</l_in_current_max>
    <l_in_current_min>-5</l_in_current_min>
    <l_abs_current_max>15</l_abs_current_max>
    <l_min_erpm>-100000</l_min_erpm>
    <l_max_erpm>100000</l_max_erpm>
    <l_erpm_start>0.8</l_erpm_start>
    <l_max_erpm_fbrake>300</l_max_erpm_fbrake>
    <l_max_erpm_fbrake_cc>1500</l_max_erpm_fbrake_cc>
    <l_min_vin>8</l_min_vin>
    <l_max_vin>40</l_max_vin>
    <l_battery_cut_start>23.8</l_battery_cut_start>
    <l_battery_cut_end>21</l_battery_cut_end>
    <l_slow_abs_current>0</l_slow_abs_current>
    <l_temp_fet_start>85</l_temp_fet_start>
    <l_temp_fet_end>90</l_temp_fet_end>
    <l_temp_motor_start>85</l_temp_motor_start>
    <l_temp_motor_end>100</l_temp_motor_end>
    <l_temp_accel_dec>0.15</l_temp_accel_dec>
    <l_min_duty>0.005</l_min_duty>
    <l_max_duty>0.95</l_max_duty>
    <l_watt_max>1.5e+06</l_watt_max>
    <l_watt_min>-1.5e+06</l_watt_min>
    <l_current_max_scale>1</l_current_max_scale>
    <l_current_min_scale>1</l_current_min_scale>
    <l_duty_start>1</l_duty_start>
    <sl_min_erpm>150</sl_min_erpm>
    <sl_min_erpm_cycle_int_limit>1100</sl_min_erpm_cycle_int_limit>
    <sl_max_fullbreak_current_dir_change>10</sl_max_fullbreak_current_dir_change>
    <sl_cycle_int_limit>62</sl_cycle_int_limit>
    <sl_phase_advance_at_br>0.8</sl_phase_advance_at_br>
    <sl_cycle_int_rpm_br>80000</sl_cycle_int_rpm_br>
    <sl_bemf_coupling_k>600</sl_bemf_coupling_k>
    <hall_table__0>-1</hall_table__0>
    <hall_table__1>1</hall_table__1>
    <hall_table__2>3</hall_table__2>
    <hall_table__3>2</hall_table__3>
    <hall_table__4>5</hall_table__4>
    <hall_table__5>6</hall_table__5>
    <hall_table__6>4</hall_table__6>
    <hall_table__7>-1</hall_table__7>
    <hall_sl_erpm>2000</hall_sl_erpm>
    <foc_current_kp>2.1884</foc_current_kp>
    <foc_current_ki>1238.79</foc_current_ki>
    <foc_f_zv>25000</foc_f_zv>
    <foc_dt_us>0.12</foc_dt_us>
    <foc_encoder_inverted>0</foc_encoder_inverted>
    <foc_encoder_offset>180</foc_encoder_offset>
    <foc_encoder_ratio>7</foc_encoder_ratio>
    <foc_encoder_sin_gain>1</foc_encoder_sin_gain>
    <foc_encoder_cos_gain>1</foc_encoder_cos_gain>
    <foc_encoder_sin_offset>1.65</foc_encoder_sin_offset>
    <foc_encoder_cos_offset>1.65</foc_encoder_cos_offset>
    <foc_encoder_sincos_filter_constant>0.5</foc_encoder_sincos_filter_constant>
    <foc_sensor_mode>2</foc_sensor_mode>
    <foc_pll_kp>2000</foc_pll_kp>
    <foc_pll_ki>30000</foc_pll_ki>
    <foc_motor_l>0.00218841</foc_motor_l>
    <foc_motor_ld_lq_diff>0.00085154</foc_motor_ld_lq_diff>
    <foc_motor_r>1.2388</foc_motor_r>
    <foc_motor_flux_linkage>0.013281</foc_motor_flux_linkage>
    <foc_observer_gain>5.67e+06</foc_observer_gain>
    <foc_observer_gain_slow>0.05</foc_observer_gain_slow>
    <foc_observer_offset>-1</foc_observer_offset>
    <foc_duty_dowmramp_kp>10</foc_duty_dowmramp_kp>
    <foc_duty_dowmramp_ki>200</foc_duty_dowmramp_ki>
    <foc_openloop_rpm>1400</foc_openloop_rpm>
    <foc_openloop_rpm_low>0</foc_openloop_rpm_low>
    <foc_d_gain_scale_start>0.9</foc_d_gain_scale_start>
    <foc_d_gain_scale_max_mod>0.2</foc_d_gain_scale_max_mod>
    <foc_sl_openloop_hyst>0.1</foc_sl_openloop_hyst>
    <foc_sl_openloop_time_lock>0</foc_sl_openloop_time_lock>
    <foc_sl_openloop_time_ramp>0.1</foc_sl_openloop_time_ramp>
    <foc_sl_openloop_time>0.05</foc_sl_openloop_time>
    <foc_hall_table__0>255</foc_hall_table__0>
    <foc_hall_table__1>167</foc_hall_table__1>
    <foc_hall_table__2>36</foc_hall_table__2>
    <foc_hall_table__3>2</foc_hall_table__3>
    <foc_hall_table__4>101</foc_hall_table__4>
    <foc_hall_table__5>135</foc_hall_table__5>
    <foc_hall_table__6>68</foc_hall_table__6>
    <foc_hall_table__7>255</foc_hall_table__7>
    <foc_hall_interp_erpm>500</foc_hall_interp_erpm>
    <foc_sl_erpm>4000</foc_sl_erpm>
    <foc_sample_v0_v7>0</foc_sample_v0_v7>
    <foc_sample_high_current>0</foc_sample_high_current>
    <foc_sat_comp>0</foc_sat_comp>
    <foc_temp_comp>0</foc_temp_comp>
    <foc_temp_comp_base_temp>25</foc_temp_comp_base_temp>
    <foc_current_filter_const>0.1</foc_current_filter_const>
    <foc_cc_decoupling>0</foc_cc_decoupling>
    <foc_observer_type>0</foc_observer_type>
    <foc_hfi_voltage_start>20</foc_hfi_voltage_start>
    <foc_hfi_voltage_run>4</foc_hfi_voltage_run>
    <foc_hfi_voltage_max>10</foc_hfi_voltage_max>
    <foc_sl_erpm_hfi>2000</foc_sl_erpm_hfi>
    <foc_hfi_start_samples>15</foc_hfi_start_samples>
    <foc_hfi_obs_ovr_sec>0.001</foc_hfi_obs_ovr_sec>
    <foc_hfi_samples>1</foc_hfi_samples>
    <foc_offsets_cal_on_boot>1</foc_offsets_cal_on_boot>
    <foc_offsets_current__0>2061.01</foc_offsets_current__0>
    <foc_offsets_current__1>2052.83</foc_offsets_current__1>
    <foc_offsets_current__2>2059.88</foc_offsets_current__2>
    <foc_offsets_voltage__0>-0.0004</foc_offsets_voltage__0>
    <foc_offsets_voltage__1>0.0011</foc_offsets_voltage__1>
    <foc_offsets_voltage__2>-0.0006</foc_offsets_voltage__2>
    <foc_offsets_voltage_undriven__0>0</foc_offsets_voltage_undriven__0>
    <foc_offsets_voltage_undriven__1>0</foc_offsets_voltage_undriven__1>
    <foc_offsets_voltage_undriven__2>0</foc_offsets_voltage_undriven__2>
    <foc_phase_filter_enable>1</foc_phase_filter_enable>
    <foc_phase_filter_max_erpm>4000</foc_phase_filter_max_erpm>
    <foc_mtpa_mode>0</foc_mtpa_mode>
    <foc_fw_current_max>0</foc_fw_current_max>
    <foc_fw_duty_start>0.9</foc_fw_duty_start>
    <foc_fw_q_current_factor>0.02</foc_fw_q_current_factor>
    <foc_fw_ramp_time>0.2</foc_fw_ramp_time>
    <gpd_buffer_notify_left>200</gpd_buffer_notify_left>
    <gpd_buffer_interpol>0</gpd_buffer_interpol>
    <gpd_current_filter_const>0.1</gpd_current_filter_const>
    <gpd_current_kp>0.03</gpd_current_kp>
    <gpd_current_ki>50</gpd_current_ki>
    <sp_pid_loop_rate>5</sp_pid_loop_rate>
    <s_pid_kp>0.004</s_pid_kp>
    <s_pid_ki>0.004</s_pid_ki>
    <s_pid_kd>0.0001</s_pid_kd>
    <s_pid_kd_filter>0.2</s_pid_kd_filter>
    <s_pid_min_erpm>900</s_pid_min_erpm>
    <s_pid_allow_braking>1</s_pid_allow_braking>
    <s_pid_ramp_erpms_s>25000</s_pid_ramp_erpms_s>
    <p_pid_kp>0.025</p_pid_kp>
    <p_pid_ki>0</p_pid_ki>
    <p_pid_kd>0</p_pid_kd>
    <p_pid_offset>0</p_pid_offset>
    <p_pid_kd_proc>0.00035</p_pid_kd_proc>
    <p_pid_kd_filter>0.2</p_pid_kd_filter>
    <p_pid_ang_div>1</p_pid_ang_div>
    <p_pid_gain_dec_angle>0</p_pid_gain_dec_angle>
    <cc_startup_boost_duty>0.01</cc_startup_boost_duty>
    <cc_min_current>0.05</cc_min_current>
    <cc_gain>0.0046</cc_gain>
    <cc_ramp_step_max>0.04</cc_ramp_step_max>
    <m_fault_stop_time_ms>500</m_fault_stop_time_ms>
    <m_duty_ramp_step>0.02</m_duty_ramp_step>
    <m_current_backoff_gain>0.5</m_current_backoff_gain>
    <m_encoder_counts>8192</m_encoder_counts>
    <m_sensor_port_mode>0</m_sensor_port_mode>
    <m_invert_direction>0</m_invert_direction>
    <m_drv8301_oc_mode>0</m_drv8301_oc_mode>
    <m_drv8301_oc_adj>16</m_drv8301_oc_adj>
    <m_bldc_f_sw_min>3000</m_bldc_f_sw_min>
    <m_bldc_f_sw_max>35000</m_bldc_f_sw_max>
    <m_dc_f_sw>25000</m_dc_f_sw>
    <m_ntc_motor_beta>3380</m_ntc_motor_beta>
    <m_out_aux_mode>0</m_out_aux_mode>
    <m_motor_temp_sens_type>0</m_motor_temp_sens_type>
    <m_ptc_motor_coeff>0.61</m_ptc_motor_coeff>
    <m_hall_extra_samples>1</m_hall_extra_samples>
    <si_motor_poles>14</si_motor_poles>
    <si_gear_ratio>1</si_gear_ratio>
    <si_wheel_diameter>0.083</si_wheel_diameter>
    <si_battery_type>0</si_battery_type>
    <si_battery_cells>7</si_battery_cells>
    <si_battery_ah>6</si_battery_ah>
    <si_motor_nl_current>1</si_motor_nl_current>
    <motor_brand>Unnamed</motor_brand>
    <motor_model>Not Specified</motor_model>
    <motor_weight>0</motor_weight>
    <motor_sensor_type>0</motor_sensor_type>
    <motor_description>&lt;!DOCTYPE HTML PUBLIC &quot;-//W3C//DTD HTML 4.0//EN&quot; &quot;http://www.w3.org/TR/REC-html40/strict.dtd&quot;&gt;
&lt;html&gt;&lt;head&gt;&lt;meta name=&quot;qrichtext&quot; content=&quot;1&quot; /&gt;&lt;style type=&quot;text/css&quot;&gt;
p, li { white-space: pre-wrap; }
&lt;/style&gt;&lt;/head&gt;&lt;body style=&quot; font-family:'Roboto'; font-size:12pt; font-weight:400; font-style:normal;&quot;&gt;
&lt;p style=&quot; margin-top:0px; margin-bottom:0px; margin-left:0px; margin-right:0px; -qt-block-indent:0; text-indent:0px;&quot;&gt;A motor description can be edited here.&lt;/p&gt;&lt;/body&gt;&lt;/html&gt;</motor_description>
    <motor_quality_bearings>0</motor_quality_bearings>
    <motor_quality_magnets>0</motor_quality_magnets>
    <motor_quality_construction>0</motor_quality_construction>
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

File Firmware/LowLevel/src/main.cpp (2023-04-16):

// Created by Clemens Elflein on 3/07/22.
// Copyright (c) 2022 Clemens Elflein. All rights reserved.
//
// This work is licensed under a Creative Commons Attribution-NonCommercial-ShareAlike 4.0 International License.
//
// Feel free to use the design in your private/educational projects, but don't try to sell the design or products based on it without getting my consent first.
//
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
//
#include <NeoPixelConnect.h>
#include <Arduino.h>
#include <FastCRC.h>
#include <PacketSerial.h>
#include "datatypes.h"
#include "hw.h"
#include "ui_board.h"
#include "imu.h"
#ifdef ENABLE_SOUND_MODULE
#include <DFPlayerMini_Fast.h>
#include <soundsystem.h>
#endif

#define IMU_CYCLETIME 20          // cycletime for refresh IMU data
#define STATUS_CYCLETIME 100      // cycletime for refresh analog and digital Statusvalues
#define UI_SET_LED_CYCLETIME 1000 // cycletime for refresh UI status LEDs

#define LIFT_EMERGENCY_MILLIS 500  // Time for wheels to be lifted in order to count as emergency. This is to filter uneven ground.
#define BUTTON_EMERGENCY_MILLIS 20 // Time for button emergency to activate. This is to debounce the button if triggered on bumpy surfaces

// Define to stream debugging messages via USB
// #define USB_DEBUG

// Only define DEBUG_SERIAL if USB_DEBUG is actually enabled.
// This enforces compile errors if it's used incorrectly.
#ifdef USB_DEBUG
#define DEBUG_SERIAL Serial
#endif
#define PACKET_SERIAL Serial1

SerialPIO uiSerial(PIN_UI_TX, PIN_UI_RX, 250);

#define UI1_SERIAL uiSerial

#define ANZ_SOUND_SD_FILES 3

// Millis after charging is retried
#define CHARGING_RETRY_MILLIS 10000

/**
 * @brief Some hardware parameters
 */
#define VIN_R1 10000.0f
#define VIN_R2 1000.0f
#define R_SHUNT 0.003f
#define CURRENT_SENSE_GAIN 100.0f

#define BATT_ABS_MAX 28.7f
#define BATT_ABS_Min 21.7f

#define BATT_FULL BATT_ABS_MAX - 0.3f
#define BATT_EMPTY BATT_ABS_Min + 0.3f

// Emergency will be engaged, if no heartbeat was received in this time frame.
#define HEARTBEAT_MILLIS 500

NeoPixelConnect p(PIN_NEOPIXEL, 1);
uint8_t led_blink_counter = 0;

PacketSerial packetSerial; // COBS communication PICO <> Raspi
PacketSerial UISerial;     // COBS communication PICO UI-Board
FastCRC16 CRC16;

#ifdef ENABLE_SOUND_MODULE
MP3Sound my_sound; // Soundsystem
#endif

unsigned long last_imu_millis = 0;
unsigned long last_status_update_millis = 0;
unsigned long last_heartbeat_millis = 0;
unsigned long last_UILED_millis = 0;

unsigned long lift_emergency_started = 0;
unsigned long button_emergency_started = 0;

// Predefined message buffers, so that we don't need to allocate new ones later.
struct ll_imu imu_message = {0};
struct ll_status status_message = {0};
// current high level state
struct ll_high_level_state last_high_level_state = {0};

// Struct for the current LEDs. This gets sent to the UI periodically
struct msg_set_leds leds_message = {0};

// A mutex which is used by core1 each time status_message is modified.
// We can lock it during message transmission to prevent core1 to modify data in this time.
auto_init_mutex(mtx_status_message);

bool emergency_latch = true;
bool sound_available = false;
bool charging_allowed = false;
bool ROS_running = false;
unsigned long charging_disabled_time = 0;

float imu_temp[9];

void sendMessage(void *message, size_t size);
void sendUIMessage(void *message, size_t size);
void onPacketReceived(const uint8_t *buffer, size_t size);
void onUIPacketReceived(const uint8_t *buffer, size_t size);
void manageUILEDS();

void setRaspiPower(bool power)
{
  // Update status bits in the status message
  status_message.status_bitmask = (status_message.status_bitmask & 0b11111101) | ((power & 0b1) << 1);
  digitalWrite(PIN_RASPI_POWER, power);
}

void updateEmergency()
{

  if (millis() - last_heartbeat_millis > HEARTBEAT_MILLIS)
  {
    emergency_latch = true;
    ROS_running = false;
  }
  uint8_t last_emergency = status_message.emergency_bitmask & 1;

  // Mask the emergency bits. 2x Lift sensor, 2x Emergency Button
  bool emergency1 = !gpio_get(PIN_EMERGENCY_1);
  bool emergency2 = !gpio_get(PIN_EMERGENCY_2);
  bool emergency3 = !gpio_get(PIN_EMERGENCY_3);
  bool emergency4 = !gpio_get(PIN_EMERGENCY_4);
  
  uint8_t emergency_state = 0;

  bool is_lifted = emergency1 || emergency2;
  bool stop_pressed = emergency3 || emergency4;

  if (is_lifted)
  {
    // We just lifted, store the timestamp
    if (lift_emergency_started == 0)
    {
      lift_emergency_started = millis();
    }
  }
  else
  {
    // Not lifted, reset the time
    lift_emergency_started = 0;
  }

  if (stop_pressed)
  {
    // We just pressed, store the timestamp
    if (button_emergency_started == 0)
    {
      button_emergency_started = millis();
    }
  }
  else
  {
    // Not pressed, reset the time
    button_emergency_started = 0;
  }

  if (lift_emergency_started > 0 && (millis() - lift_emergency_started) >= LIFT_EMERGENCY_MILLIS)
  {
    // Emergency bit 2 (lift wheel 1)set?
    if (emergency1)
      emergency_state |= 0b01000;
    // Emergency bit 1 (lift wheel 2)set?
    if (emergency2)
      emergency_state |= 0b10000;
  }

  if (button_emergency_started > 0 && (millis() - button_emergency_started) >= BUTTON_EMERGENCY_MILLIS)
  {
    // Emergency bit 2 (stop button) set?
    if (emergency3)
      emergency_state |= 0b00010;
    // Emergency bit 1 (stop button)set?
    if (emergency4)
      emergency_state |= 0b00100;
  }

  if (emergency_state || emergency_latch)
  {
    emergency_latch |= 1;
    emergency_state |= 1;
  }

  status_message.emergency_bitmask = emergency_state;

  // If it's a new emergency, instantly send the message. This is to not spam the channel during emergencies.
  if (last_emergency != (emergency_state & 1))
  {
    sendMessage(&status_message, sizeof(struct ll_status));

    // Update LEDs instantly
    manageUILEDS();
  }
}

// deals with the pyhsical information an control the UI-LEDs und buzzer in depency of voltage und current values
void manageUILEDS()
{
  // Show Info Docking LED
  if ((status_message.charging_current > 0.80f) && (status_message.v_charge > 20.0f))
    setLed(leds_message, LED_CHARGING, LED_blink_fast);
  else if ((status_message.charging_current <= 0.80f) && (status_message.charging_current >= 0.15f) && (status_message.v_charge > 20.0f))
    setLed(leds_message, LED_CHARGING, LED_blink_slow);
  else if ((status_message.charging_current < 0.15f) && (status_message.v_charge > 20.0f))
    setLed(leds_message, LED_CHARGING, LED_on);
  else
    setLed(leds_message, LED_CHARGING, LED_off);

  // Show Info Battery state
  if (status_message.v_battery >= (BATT_EMPTY + 2.0f))
    setLed(leds_message, LED_BATTERY_LOW, LED_off);
  else
    setLed(leds_message, LED_BATTERY_LOW, LED_on);

  if (status_message.v_charge < 10.0f) // activate only when undocked
  {
    // use the first LED row as bargraph
    setBars7(leds_message, status_message.batt_percentage / 100.0);
    if (last_high_level_state.gps_quality == 0)
    {
      // if quality is 0, flash all LEDs to notify the user to calibrate.
      setBars4(leds_message, -1.0);
    }
    else
    {
      setBars4(leds_message, last_high_level_state.gps_quality / 100.0);
    }
  }
  else
  {
    setBars7(leds_message, 0);
    setBars4(leds_message, 0);
  }

  if(last_high_level_state.gps_quality < 25) {
    setLed(leds_message, LED_POOR_GPS, LED_on);
  } else if(last_high_level_state.gps_quality < 50) {
    setLed(leds_message, LED_POOR_GPS, LED_blink_fast);
  } else if(last_high_level_state.gps_quality < 75) {
    setLed(leds_message, LED_POOR_GPS, LED_blink_slow);
  } else {
    setLed(leds_message, LED_POOR_GPS, LED_off);
  }

  // Let S1 show if ros is connected and which state it's in
  if (!ROS_running)
  {
    setLed(leds_message, LED_S1, LED_off);
  }
  else
  {
    switch (last_high_level_state.current_mode & 0b111111)
    {
    case HighLevelMode::MODE_IDLE:
      setLed(leds_message, LED_S1, LED_on);
      break;
    case HighLevelMode::MODE_AUTONOMOUS:
      setLed(leds_message, LED_S1, LED_blink_slow);
      break;
    default:
      setLed(leds_message, LED_S1, LED_blink_fast);
      break;
    }
    switch ((last_high_level_state.current_mode >> 6) & 0b11)
    {
    case 1:
      setLed(leds_message, LED_S2, LED_blink_slow);
      break;
    case 2:
      setLed(leds_message, LED_S2, LED_blink_fast);
      break;
    case 3:
      setLed(leds_message, LED_S2, LED_on);
      break;
    default:
      setLed(leds_message, LED_S2, LED_off);
      break;
    }
  }

  // Show Info mower lifted or stop button pressed
  if (status_message.emergency_bitmask & 0b00110)
  {
    setLed(leds_message, LED_MOWER_LIFTED, LED_blink_fast);
  }
  else if (status_message.emergency_bitmask & 0b11000)
  {
    setLed(leds_message, LED_MOWER_LIFTED, LED_blink_slow);
  }
  else if (status_message.emergency_bitmask & 0b0000001)
  {
    setLed(leds_message, LED_MOWER_LIFTED, LED_on);
  }
  else
  {
    setLed(leds_message, LED_MOWER_LIFTED, LED_off);
  }

  sendUIMessage(&leds_message, sizeof(leds_message));
}

void setup1()
{
  // Core
  digitalWrite(LED_BUILTIN, HIGH);
}

void loop1()
{
  // Loop through the mux and query actions. Store the result in the multicore fifo
  for (uint8_t mux_address = 0; mux_address < 7; mux_address++)
  {
    gpio_put_masked(0b111 << 13, mux_address << 13);
    delay(1);
    bool state = gpio_get(PIN_MUX_IN);

    switch (mux_address)
    {
    case 5:
      mutex_enter_blocking(&mtx_status_message);

      if (state)
      {
        status_message.status_bitmask |= 0b00010000;
      }
      else
      {
        status_message.status_bitmask &= 0b11101111;
      }
      mutex_exit(&mtx_status_message);

      break;
    case 6:
      mutex_enter_blocking(&mtx_status_message);
      if (state)
      {
        status_message.status_bitmask |= 0b00100000;
      }
      else
      {
        status_message.status_bitmask &= 0b11011111;
      }
      mutex_exit(&mtx_status_message);
      break;
    default:
      break;
    }
  }

  delay(100);
}

void setup()
{
  // Setup the correct pin mux for the hardware.
  hw_assign_pins();

  //  We do hardware init in this core, so that we don't get invalid states.
  //  Therefore, we pause the other core until setup() was a success
  rp2040.idleOtherCore();

  emergency_latch = true;
  ROS_running = false;

  lift_emergency_started = 0;
  button_emergency_started = 0;
  // Initialize messages
  imu_message = {0};
  status_message = {0};
  imu_message.type = PACKET_ID_LL_IMU;
  status_message.type = PACKET_ID_LL_STATUS;

  // Setup pins
  pinMode(LED_BUILTIN, OUTPUT);
  pinMode(PIN_ENABLE_CHARGE, OUTPUT);
  digitalWrite(PIN_ENABLE_CHARGE, LOW);

  gpio_init(PIN_RASPI_POWER);
  gpio_put(PIN_RASPI_POWER, true);
  gpio_set_dir(PIN_RASPI_POWER, true);
  gpio_put(PIN_RASPI_POWER, true);

  // Enable raspi power
  p.neoPixelSetValue(0, 32, 0, 0, true);
  delay(1000);
  setRaspiPower(true);
  p.neoPixelSetValue(0, 255, 0, 0, true);

  pinMode(PIN_MUX_OUT, OUTPUT);
  pinMode(PIN_MUX_ADDRESS_0, OUTPUT);
  pinMode(PIN_MUX_ADDRESS_1, OUTPUT);
  pinMode(PIN_MUX_ADDRESS_2, OUTPUT);

  pinMode(PIN_EMERGENCY_1, INPUT);
  pinMode(PIN_EMERGENCY_2, INPUT);
  pinMode(PIN_EMERGENCY_3, INPUT);
  pinMode(PIN_EMERGENCY_4, INPUT);

  analogReadResolution(12);

#ifdef USB_DEBUG
  DEBUG_SERIAL.begin(115200);
#endif

  // init serial com to RasPi
  PACKET_SERIAL.begin(115200);
  packetSerial.setStream(&PACKET_SERIAL);
  packetSerial.setPacketHandler(&onPacketReceived);

  UI1_SERIAL.begin(115200);
  UISerial.setStream(&UI1_SERIAL);
  UISerial.setPacketHandler(&onUIPacketReceived);

  /*
   * IMU INITIALIZATION
   */

  if (!init_imu())
  {
#ifdef USB_DEBUG
    DEBUG_SERIAL.println("IMU initialization unsuccessful");
    DEBUG_SERIAL.println("Check IMU wiring or try cycling power");
#endif
    status_message.status_bitmask = 0;
    while (1)
    {
      p.neoPixelSetValue(0, 255, 0, 0, true);
      delay(500);
      p.neoPixelSetValue(0, 0, 0, 0, true);
      delay(500);
    }

    {
#ifdef USB_DEBUG
      DEBUG_SERIAL.println("Error: Imu init failed");
#endif
      // We don't need to lock the mutex here, since core 1 is sleeping anyways
      sendMessage(&status_message, sizeof(struct ll_status));
      delay(1000);
    }
  }

#ifdef USB_DEBUG
  DEBUG_SERIAL.println("Imu initialized");
#endif

  /*
   * /IMU INITIALIZATION
   */

  status_message.status_bitmask |= 1;

#ifdef ENABLE_SOUND_MODULE
  p.neoPixelSetValue(0, 0, 255, 255, true);

  sound_available = my_sound.begin();
  if (sound_available)
  {
    p.neoPixelSetValue(0, 0, 0, 255, true);
    my_sound.setvolume(100);
    my_sound.playSoundAdHoc(1);
    p.neoPixelSetValue(0, 255, 255, 0, true);
  }
  else
  {
    for (uint8_t b = 0; b < 3; b++)
    {
      p.neoPixelSetValue(0, 0, 0, 0, true);
      delay(200);
      p.neoPixelSetValue(0, 0, 0, 255, true);
      delay(200);
    }
  }


#else
  sound_available = false;
#endif

  rp2040.resumeOtherCore();

  // UIboard clear all LEDs
  leds_message.type = Set_LEDs;
  leds_message.leds = 0;
  sendUIMessage(&leds_message, sizeof(leds_message));
}

void onUIPacketReceived(const uint8_t *buffer, size_t size)
{

  u_int16_t *crc_pointer = (uint16_t *)(buffer + (size - 2));
  u_int16_t readcrc = *crc_pointer;

  // check structure size
  if (size < 4)
    return;

  // check the CRC
  uint16_t crc = CRC16.ccitt(buffer, size - 2);

  if (buffer[size - 1] != ((crc >> 8) & 0xFF) ||
      buffer[size - 2] != (crc & 0xFF))
    return;

  if(buffer[0] == Get_Button && size == sizeof(struct msg_event_button)) {
    struct msg_event_button* msg = (struct msg_event_button*)buffer;
    struct ll_ui_event ui_event;
    ui_event.type = PACKET_ID_LL_UI_EVENT;
    ui_event.button_id = msg->button_id;
    ui_event.press_duration = msg->press_duration;
    sendMessage(&ui_event, sizeof(ui_event));
  }
}

void onPacketReceived(const uint8_t *buffer, size_t size)
{
  // sanity check for CRC to work (1 type, 1 data, 2 CRC)
  if (size < 4)
    return;

  // check the CRC
  uint16_t crc = CRC16.ccitt(buffer, size - 2);

  if (buffer[size - 1] != ((crc >> 8) & 0xFF) ||
      buffer[size - 2] != (crc & 0xFF))
    return;

  if (buffer[0] == PACKET_ID_LL_HEARTBEAT && size == sizeof(struct ll_heartbeat))
  {

    // CRC and packet is OK, reset watchdog
    last_heartbeat_millis = millis();
    ROS_running = true;
    struct ll_heartbeat *heartbeat = (struct ll_heartbeat *)buffer;
    if (heartbeat->emergency_release_requested)
    {
      emergency_latch = false;
    }
    // Check in this order, so we can set it again in the same packet if required.
    if (heartbeat->emergency_requested)
    {
      emergency_latch = true;
    }
  }
  else if (buffer[0] == PACKET_ID_LL_HIGH_LEVEL_STATE && size == sizeof(struct ll_high_level_state))
  {
    // copy the state
    last_high_level_state = *((struct ll_high_level_state *)buffer);
  }
}

// returns true, if it's a good idea to charge the battery (current, voltages, ...)
bool checkShouldCharge()
{
  return status_message.v_charge < 30.0 && status_message.charging_current < 1.5 && status_message.v_battery < 29.0;
}

void updateChargingEnabled()
{
  if (charging_allowed)
  {
    if (!checkShouldCharge())
    {
      digitalWrite(PIN_ENABLE_CHARGE, LOW);
      charging_allowed = false;
      charging_disabled_time = millis();
    }
  }
  else
  {
    // enable charging after CHARGING_RETRY_MILLIS
    if (millis() - charging_disabled_time > CHARGING_RETRY_MILLIS)
    {
      if (!checkShouldCharge())
      {
        digitalWrite(PIN_ENABLE_CHARGE, LOW);
        charging_allowed = false;
        charging_disabled_time = millis();
      }
      else
      {
        digitalWrite(PIN_ENABLE_CHARGE, HIGH);
        charging_allowed = true;
      }
    }
  }
}

void updateNeopixel()
{
  led_blink_counter++;
  // flash red on emergencies
  if (emergency_latch && led_blink_counter & 0b10)
  {
    p.neoPixelSetValue(0, 128, 0, 0, true);
  }
  else
  {
    if (ROS_running)
    {
      // Green, if ROS is running
      p.neoPixelSetValue(0, 0, 255, 0, true);
    }
    else
    {
      // Yellow, if it's not running
      p.neoPixelSetValue(0, 255, 50, 0, true);
    }
  }
}

void loop()
{
  packetSerial.update();
  UISerial.update();
  imu_loop();
  updateChargingEnabled();
  updateEmergency();

  unsigned long now = millis();
  if (now - last_imu_millis > IMU_CYCLETIME)
  {
    // we have to copy to the temp data structure due to alignment issues
    imu_read(imu_temp, imu_temp + 3, imu_temp + 6);
    imu_message.acceleration_mss[0] = imu_temp[0];
    imu_message.acceleration_mss[1] = imu_temp[1];
    imu_message.acceleration_mss[2] = imu_temp[2];
    imu_message.gyro_rads[0] = imu_temp[3];
    imu_message.gyro_rads[1] = imu_temp[4];
    imu_message.gyro_rads[2] = imu_temp[5];
    imu_message.mag_uT[0] = imu_temp[6];
    imu_message.mag_uT[1] = imu_temp[7];
    imu_message.mag_uT[2] = imu_temp[8];

    imu_message.dt_millis = now - last_imu_millis;
    sendMessage(&imu_message, sizeof(struct ll_imu));

    last_imu_millis = now;
  }

  if (now - last_status_update_millis > STATUS_CYCLETIME)
  {
    updateNeopixel();

    status_message.v_battery = (float)analogRead(PIN_ANALOG_BATTERY_VOLTAGE) * (3.3f / 4096.0f) * ((VIN_R1 + VIN_R2) / VIN_R2);
    status_message.v_charge = (float)analogRead(PIN_ANALOG_CHARGE_VOLTAGE) * (3.3f / 4096.0f) * ((VIN_R1 + VIN_R2) / VIN_R2);
    status_message.charging_current = (float)analogRead(PIN_ANALOG_CHARGE_CURRENT) * (3.3f / 4096.0f) / (CURRENT_SENSE_GAIN * R_SHUNT);
    status_message.status_bitmask = (status_message.status_bitmask & 0b11111011) | ((charging_allowed & 0b1) << 2);
    status_message.status_bitmask = (status_message.status_bitmask & 0b11011111) | ((sound_available & 0b1) << 5);

    // calculate percent value accu filling
    float delta = BATT_FULL - BATT_EMPTY;
    float vo = status_message.v_battery - BATT_EMPTY;
    status_message.batt_percentage = vo / delta * 100;
    if (status_message.batt_percentage > 100)
      status_message.batt_percentage = 100;

    mutex_enter_blocking(&mtx_status_message);
    sendMessage(&status_message, sizeof(struct ll_status));
    mutex_exit(&mtx_status_message);

    last_status_update_millis = now;
#ifdef USB_DEBUG
    DEBUG_SERIAL.print("status: 0b");
    DEBUG_SERIAL.print(status_message.status_bitmask, BIN);
    DEBUG_SERIAL.print("\t");

    DEBUG_SERIAL.print("vin: ");
    DEBUG_SERIAL.print(status_message.v_battery, 3);
    DEBUG_SERIAL.print(" V\t");
    DEBUG_SERIAL.print("vcharge: ");
    DEBUG_SERIAL.print(status_message.v_charge, 3);
    DEBUG_SERIAL.print(" V\t");
    DEBUG_SERIAL.print("charge_current: ");
    DEBUG_SERIAL.print(status_message.charging_current, 3);
    DEBUG_SERIAL.print(" A\t");
    DEBUG_SERIAL.print("emergency: 0b");
    DEBUG_SERIAL.print(status_message.emergency_bitmask, BIN);
    DEBUG_SERIAL.println();
#endif
  }

  if (now - last_UILED_millis > UI_SET_LED_CYCLETIME)
  {
    manageUILEDS();
    last_UILED_millis = now;
#ifdef ENABLE_SOUND_MODULE
    if (sound_available)
    {
      my_sound.processSounds();
    }
#endif
  }
}

void sendMessage(void *message, size_t size)
{
  // Only send messages, if ROS is running, else Raspi sometimes doesn't boot
  if (!ROS_running)
    return;

  // packages need to be at least 1 byte of type, 1 byte of data and 2 bytes of CRC
  if (size < 4)
  {
    return;
  }
  uint8_t *data_pointer = (uint8_t *)message;

  // calculate the CRC
  uint16_t crc = CRC16.ccitt((uint8_t *)message, size - 2);
  data_pointer[size - 1] = (crc >> 8) & 0xFF;
  data_pointer[size - 2] = crc & 0xFF;

  packetSerial.send((uint8_t *)message, size);
}

void sendUIMessage(void *message, size_t size)
{
  // packages need to be at least 1 byte of type, 1 byte of data and 2 bytes of CRC
  if (size < 4)
  {
    return;
  }
  uint8_t *data_pointer = (uint8_t *)message;

  // calculate the CRC
  uint16_t crc = CRC16.ccitt((uint8_t *)message, size - 2);
  data_pointer[size - 1] = (crc >> 8) & 0xFF;
  data_pointer[size - 2] = crc & 0xFF;

  UISerial.send((uint8_t *)message, size);
}

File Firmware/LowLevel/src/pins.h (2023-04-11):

#pragma once

#ifdef HW_0_9_X
#define PIN_IMU_CS 17
#define PIN_ANALOG_BATTERY_VOLTAGE 27
#define PIN_ANALOG_CHARGE_VOLTAGE 26
#define PIN_ANALOG_CHARGE_CURRENT 28

#define PIN_ENABLE_CHARGE 22

#define PIN_ESC_SHUTDOWN 20
#define PIN_RASPI_POWER 21

#define PIN_EMERGENCY_1 7
#define PIN_EMERGENCY_2 6
#define PIN_EMERGENCY_3 3
#define PIN_EMERGENCY_4 2

#define PIN_MUX_IN 11
#define PIN_MUX_OUT 12
#define PIN_MUX_ADDRESS_0 13
#define PIN_MUX_ADDRESS_1 14
#define PIN_MUX_ADDRESS_2 15

#define PIN_NEOPIXEL 10

#define PIN_UI_TX 4
#define PIN_UI_RX 5

#ifdef ENABLE_SOUND_MODULE
#define PIN_SOUND_TX 8
#define PIN_SOUND_RX 9
#endif

#ifdef WT901_INSTEAD_OF_SOUND
    #ifdef ENABLE_SOUND_MODULE
        #error you can not enable sound and have wt901 on sound port at the same time.
    #endif
    #define PIN_WT901_TX 8
    #define PIN_WT901_RX 9
#elif WT901 //This is to use WT901 on MPU9250 Slot via Serial.
    #define PIN_WT901_TX 17
    #define PIN_WT901_RX 16
#endif

#elif HW_0_10_X || HW_0_11_X || HW_0_12_X
#define WT901_WIRE Wire

#define PIN_WT901_SDA 8
#define PIN_WT901_SCL 9

#define PIN_IMU_CS 9
#define PIN_IMU_MOSI 7
#define PIN_IMU_MISO 8
#define PIN_IMU_SCK 6

#define PIN_ANALOG_BATTERY_VOLTAGE 27
#define PIN_ANALOG_CHARGE_VOLTAGE 26
#define PIN_ANALOG_CHARGE_CURRENT 28

#define PIN_ENABLE_CHARGE 22

#define PIN_ESC_SHUTDOWN 20
#define PIN_RASPI_POWER 21

#define PIN_EMERGENCY_1 18
#define PIN_EMERGENCY_2 19
#define PIN_EMERGENCY_3 3
#define PIN_EMERGENCY_4 2

#define PIN_MUX_IN 11
#define PIN_MUX_OUT 12
#define PIN_MUX_ADDRESS_0 13
#define PIN_MUX_ADDRESS_1 14
#define PIN_MUX_ADDRESS_2 15

#define PIN_NEOPIXEL 10

#define PIN_UI_TX 4
#define PIN_UI_RX 5

#ifdef ENABLE_SOUND_MODULE
#define PIN_SOUND_TX 16
#define PIN_SOUND_RX 17
#endif

#else
#error No hardware version defined
#endif

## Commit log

2022-01-26 wip schematic
    [GPS.kicad_sch, IMU.kicad_sch, OpenMowerMainboard.kicad_pcb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]
2022-01-26 removed unused io expander
    [MCP23S08-E_SS.step, OpenMowerMainboard.kicad_sch]
2022-01-27 added footprints to schematic
    [GPS.kicad_sch, LEVEL_SHIFTER.kicad_sch, OpenMowerMainboard.kicad_pcb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]
2022-01-30 wip pcb layout
    [OpenMowerMainboard.kicad_pcb, OpenMowerMainboard.kicad_sch, RobotConnectors.kicad_sch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]
2022-01-31 routing mostly done
    [OpenMowerMainboard.kicad_pcb, OpenMowerMainboard.kicad_sch, RobotConnectors.kicad_sch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]
2022-01-31 v1.0 release candidate
    [OpenMowerMainboard.kicad_pcb]
2022-01-31 minor changes
    [LEVEL_SHIFTER.kicad_sch, mosfet_switch.kicad_sch]
2022-02-26 update Resistance Values
    [LEVEL_SHIFTER.kicad_sch, OpenMowerMainboard.kicad_sch, RaspberryPi.kicad_sch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]
2022-03-04 added todos, added image of current mainboard
    [LEVEL_SHIFTER.kicad_sch, OpenMowerMainboard.kicad_sch, mosfet_switch.kicad_sch]
2022-03-04 Added default pull down, raspberry pi power override and some TODOs
    [GPS.kicad_sch, OpenMowerMainboard.kicad_sch, RaspberryPi.kicad_sch]
2022-03-09 redirect_serial.sh now redirects all motor serials to tcp port 2101, 2102 and 2103
2022-03-10 Base firmware works so far. IMU, emergency, voltages and current measurement works.
2022-03-16 Low Level board can now talk to ROS; Heartbeat with timeout and emergency mode works
2022-03-18 Added motor configuration for YardForce Classic 500; Fixed gitignore
    [YardForce_Classic_Drive_App.xml, YardForce_Classic_Drive_Motor.xml, YardForce_Classic_Mower_App.xml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]
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2022-04-06 WIP hardware revision
    [GPS.kicad_sch, OpenMowerMainboard.kicad_pcb, OpenMowerMainboard.kicad_sch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]
2022-04-07 v0_9_1 mainboard rework
    [GPS.kicad_sch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]
2022-04-10 small PCB changes
    [GPS.kicad_sch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]
2022-04-24 added some valued, exported iBOM
    [OpenMowerMainboard.kicad_sch, RobotConnectors.kicad_sch, dcdc.kicad_sch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]
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2022-04-28 fixed xESC motor configs
    [YardForce_Classic_Drive_Motor.xml, YardForce_Classic_Mower_Motor.xml]
2022-05-05 swapped pins, moved voltage solder jumper to the bottom, removed C24 since it was optional anyways.
    [OpenMowerMainboard.kicad_sch, RobotConnectors.kicad_sch, dcdc.kicad_sch]
2022-05-07 BoM data added to kicad - results exported to .xlsx file
    [GPS.kicad_sch, IMU.kicad_sch, LEVEL_SHIFTER.kicad_sch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]
2022-05-07 Fuse holders and aternative led led pn from lcsc added
    [OpenMowerMainboard.kicad_sch, RobotConnectors.kicad_sch]
2022-05-12 update bom error
    [OpenMowerMainboard.kicad_sch, dcdc.kicad_sch]
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2022-05-18 Revert "LowLevelboard interface to UI-board integrated"
    This reverts commit ba8099bdfa153b7a3b7ce462b003457200ab419c.
    [main.cpp]
2022-05-20 BOM changes
    [GPS.kicad_sch, LEVEL_SHIFTER.kicad_sch, OpenMowerMainboard.kicad_sch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]
2022-05-20 added jumper for assembly without sound and ultrasonic sensors
    [OpenMowerMainboard-B_Cu.gbr, OpenMowerMainboard-B_Mask.gbr, OpenMowerMainboard-B_Paste.gbr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]
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2022-06-07 Emergency Timing and fix
    [main.cpp]
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2022-06-17 fixed BOM
    [dcdc.kicad_sch]
2022-06-24 Automatic generation of bom/render/gerbers (#21)
    * feat(GH): KiBot releases
    * fix: file case to match project
    * feat(GH): drc,erc,version,navigator,2d render
    * feat(GH): drc,erc on push, GH pages on tag
    [IMU.kicad_sch, imu.kicad_sch]
2022-06-24 removed bom and gerbers, will be generated automatically from now on.
    [OpenMowerMainboard_bom_.csv]
2022-06-26 added motor configs for SA650ECO
    [YardForce_SA650ECO_Drive_Motor.xml, YardForce_SA650ECO_Mower_Motor.xml]
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2022-07-19 fixed build for non-sound environment
    [main.cpp]
2022-07-19 correct serial for status updates
    [main.cpp]
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2022-08-01 fix(bom): custom filter to match kicad built-in + schematic PDF (#25)
    * fix(bom): custom filter to match kicad built-in
    * docs: include PDF schematic in auto-generator
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2022-08-09 fix(soundmodule): female socket instead of male headers
    [OpenMowerMainboard.kicad_sch, sound_module.kicad_sch]
2022-08-09 fix(motorsensor): J10 was upside-down
    [RobotConnectors.kicad_sch]
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2022-08-19 Fixes from Vermut's 1st batch (#28)
    * fix(soundmodule): female socket instead of male headers
    * fix(motorsensor): J10 was upside-down
    * feat(pcb): rotate J10 and move lower, soundboard pin sockets
    * feat(pcb): add a corner line on a silkscreen for neopixel
    [OpenMowerMainboard.kicad_sch, RobotConnectors.kicad_sch, sound_module.kicad_sch]
2022-08-20 feat(bom): added compatible lcsc codes, updated discontinued ones
    [RobotConnectors.kicad_sch, dcdc.kicad_sch, opamps.kicad_sch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]
2022-08-20 chore: save schematics and update PCB to sync in-line changes
    [LEVEL_SHIFTER.kicad_sch, opamps.kicad_sch]
2022-08-20 fix(pcb): replace KISYS3DMOD with v6's KICAD6_3DMODEL_DIR
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2022-08-23 feat(imu): switch GPIO pins 6-9 with 16-19
    allows to use both MPU9250 and WT901 on the same header by routing UART pins to IMU header
    [pico.kicad_sch]
2022-08-23 fix: fixed ERC/DRC errors, removed LM2596S
    [GPS.kicad_sch, OpenMowerMainboard.kicad_sch, RobotConnectors.kicad_sch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]
2022-08-23 fix(motorsensor): replace PN for J10 with C442247
    [RobotConnectors.kicad_sch]
2022-08-23 chore: remove space before PN
    [RaspberryPi.kicad_sch, imu.kicad_sch]
2022-08-28 feat(imu): additional pin header for WT901
    [OpenMowerMainboard.kicad_sch, imu.kicad_sch]
2022-08-31 fix(imu): update and reroute sound/imu connections
    [GPS.kicad_sch, OpenMowerMainboard.kicad_sch, RaspberryPi.kicad_sch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]
2022-08-31 feat(Pico/W): update symbol and schematic
    [OpenMowerMainboard.kicad_sch, pico.kicad_sch]
2022-08-31 fix(imu): fix tracks, update Pico footprint
    for future compatibility with PicoW
    [pico.kicad_sch]
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2022-09-11 feat(imu): ttl/i2c selector for WT901
    + moved voltage selector for sound
    [GPS.kicad_sch, OpenMowerMainboard.kicad_sch, RaspberryPi.kicad_sch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]
2022-09-25 fix(imu): move WT901 to the right due to PCB clamp overlap
2022-09-25 chore(imu): silence the overlap DRC error
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2022-11-03 fix: swapped stop and lift sensors since they were swapped
    [main.cpp]
2022-11-07 fix: gyro sign
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2022-11-12 feat: fixed soundsystem, fixed emergency switches for 0.10.x hardware
    [main.cpp, soundsystem.cpp]
2022-11-18 fix: emergency switches were inverted
    [main.cpp]
2022-11-25 feat: rearrange WT901, switch to SMD, extend pads
    Fixes #37
2022-11-25 fix: put back Pico-Dev pin names
    Fixes #44
2022-11-25 chore: annotate non-annotated symbols
    [OpenMowerMainboard.kicad_sch, imu.kicad_sch]
2022-11-25 feat: add SW1 RPi power-on switch
    Fixes #40
    [RaspberryPi.kicad_sch]
2022-12-03 feat: remove C4 from board (no space)
    [escs.kicad_sch]
2022-12-03 fix: add switch courtyard
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2022-12-03 chore: duplicate `LCSC Part` to LCSC
    [RaspberryPi.kicad_sch]
2022-12-03 fix: removed useless ground vias, moved traces to widen the VBATT trace again, fixed ground plane stitching
2022-12-06 feat: update RPi4 40 pin footprint with pcb holes
    Fixes #38
2022-12-09 feat(dock): add original dockstation designs as-is
    [mower_PowerDeviceCarrier.kicad_pcb, mower_PowerDeviceCarrier.kicad_sch]
2022-12-09 chore(dock): de translations
    [mower_PowerDeviceCarrier.kicad_pcb]
2022-12-09 fix(dock): move led pin header to avoid screw hole overlap
    [mower_PowerDeviceCarrier.kicad_pcb]
2022-12-09 feat(dock): add 3.81mm terminals and pinholes to connect to dc/dc terminal
    [mower_PowerDeviceCarrier.kicad_pcb, mower_PowerDeviceCarrier.kicad_sch]
2022-12-09 fix(dock): erc/drc
    [mower_PowerDeviceCarrier.kicad_pcb, mower_PowerDeviceCarrier.kicad_sch]
2022-12-09 feat(dock): make bolt holes M3 (3.1mm)
    3M is much easier to source
    [mower_PowerDeviceCarrier.kicad_pcb]
2022-12-09 feat(dock): make mount holes 2.5mm instead of 4.5mm (radius)
    [mower_PowerDeviceCarrier.kicad_pcb]
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2023-02-07 fix: exclude C3, C6 from BOM
2023-02-16 feat(ui): add initial UI board
    [CoverUI.kicad_pcb, CoverUI.kicad_sch, LEDmux.kicad_sch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]
2023-02-16 feat: added LSM6DSO as IMU
    [LSM6DSOTR.stp, OpenMowerMainboard.kicad_sch, imu.kicad_sch]
2023-02-17 chore: cleanup pcb, rearrange labels, add LCSC code
    [GPS.kicad_sch, OpenMowerMainboard.kicad_sch, RaspberryPi.kicad_sch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]
2023-02-17 feat(imu): deprecate WT901 and MPU9250 (J20)
    [OpenMowerMainboard.kicad_sch, RaspberryPi.kicad_sch, imu.kicad_sch]
2023-02-17 feat(sound): deprecate DFplayer (R7,R13,J17,J23)
    [sound_module.kicad_sch]
2023-02-17 feat(bom): update LCSC codes
    [GPS.kicad_sch, LEVEL_SHIFTER.kicad_sch, OpenMowerMainboard.kicad_sch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]
2023-02-17 fix(erc): remove unconnected SDA, SDL from WT901
    [GPS.kicad_sch, OpenMowerMainboard.kicad_sch, RaspberryPi.kicad_sch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]
2023-02-17 fix(drc): remove duplicate via
    [CoverUI.kicad_pcb]
2023-02-26 fix(ui): update switch footprints, make central hole smaller
    [CoverUI.kicad_pcb, CoverUI.kicad_sch, Switch.kicad_sch]
2023-03-07 fix: R11 notation 53k6
    [OpenMowerMainboard.kicad_sch, dcdc.kicad_sch]
2023-03-07 fix: remove "Exclude from BOM" items from POS
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2023-03-07 fix(ui): connect 3.3V to 3V3
    [CoverUI.kicad_pcb, CoverUI.kicad_sch, LEDmux.kicad_sch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]
2023-03-19 fix: fixed units for IMU
2023-03-20 fix(ui): update switches to 4.5mm
    [CoverUI.kicad_pcb, CoverUI.kicad_sch, LEDmux.kicad_sch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]
2023-03-21 fix(mb): swap pico GP4,5 with GP8,9
    [GPS.kicad_sch, OpenMowerMainboard.kicad_sch, RaspberryPi.kicad_sch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]
2023-03-21 fix: IMU values were off by a factor of 1000.0
2023-03-23 feat(mb): add pin header for RPi force power
    [OpenMowerMainboard.kicad_sch, RaspberryPi.kicad_sch]
2023-04-15 chore: move hardware specific stuff into own files to avoid a very complex pins.h
    [hw_0_10_11_12.h, hw_0_13.h, hw_0_9.h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]

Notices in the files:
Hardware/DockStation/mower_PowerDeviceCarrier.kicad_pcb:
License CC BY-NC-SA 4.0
